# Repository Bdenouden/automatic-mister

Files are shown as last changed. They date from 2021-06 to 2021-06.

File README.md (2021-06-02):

# Mister automatic
An automated approach to misting my mushroom farm

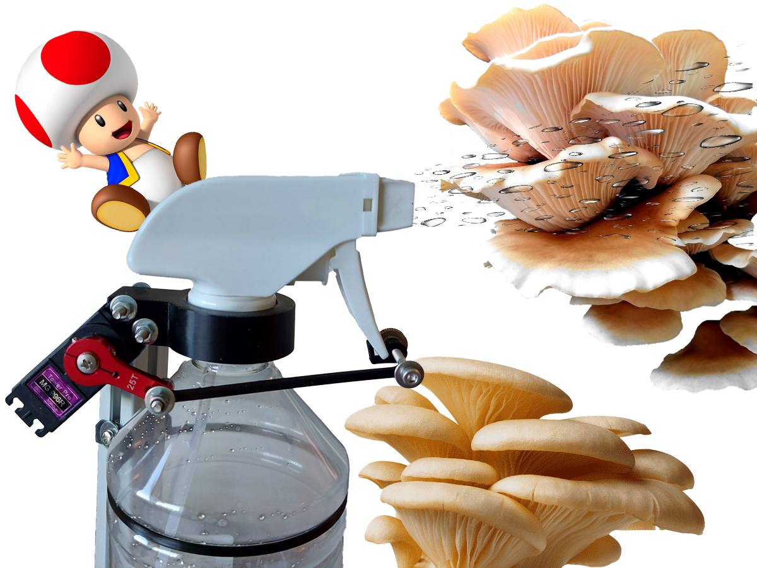
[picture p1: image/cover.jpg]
cover


## Introduction
For my birthday this year, I've received my own mushroom farm. 
This farm starts out as a block of mycelium but promises to turn into edible mushrooms in approximately 10 days. 
In order to do so, the mycelium should first be submersed in water for a couple of hours and misted twice a day until the mushrooms are ready. 
When starting this farm I completely forgot my upcoming 4 days away from home, which would most likely mean my mushroom farm would dry out.

Since it was too late to postpone the farm, a different solution had to be found to mist my mushrooms whilst I was away from home. 
Furthermore a solution had to be found and created within 4 days so there was no time to order new components.

## Design
The biggest problem was the amount of force required to activate the spray nozzle. The motor must obviously have enough torque but at the same time, the bottle should not move when the motor is activated.

Speaking of activation: this system should mist my mushrooms twice a day and each time it activates a couple of 'pumps' are required.
Preferably, there would also be a feedback to the user like emails or notifications to existing home automation sytems.
To obtain this behaviour, a wifi enabled microprocessor is required along with a small pcb to manage power distribution.

This problem is therefore divided into thre separate issues: 
- Selecting a sufficiently strong motor
- Designing a robust, preferably self-supporting system
- Controlling the system

At the end of this section, a proof of concept is evaluated. 

### Motor
To solve the first issue, the MG996R servo motor was used; a high torque metal gear servo. Although this motor has sufficient torque (11kg/cm @ 6V), it can draw up to 2.5A of current.

The servo horn I had available is a metal arm with a maximum arm of 2.5cm, reducing the max torque to 4.4kg.
A quick test using a portable luggage scale was performed to verify if this would be enough. 
Since approximately 2 kg is required to fully retract the spray nozzle arm, the combination of the MG996R servo motor and 2.5cm servo horn should be strong enough.

Besides the 6V stall torque, the 4.8V stall torque was also specified by the manufacturer: 9.4kg/cm.
Using a 5V source and the same 2.5cm servo horn should still result in a max torque of ~3.8kg. 

This is very usefull information since I don't have any 6V sources which can supply up to 2.5A laying around but I do have many 5V usb chargers which can easily handle up to 3A.

### CAD
The second problem had to be solved using CAD. To prevent the bottle moving when spraying, the force used to activate the spray had to come from a part which is attached to the spray head but does not move during spraying.
By manually spraying a bit, I figured the most sturdy part which satisfies above demands would be the screwcap of the bottle.

The body of the system was thus designed to mimic how a human holds the spray bottle but with some attachements added for the selected servo motor. 
The image below shows the assembly of the cad model and the servo motor.

In order to attach the servo horn to the spray lever, a small clip which just snaps onto said lever and an arm to couple the clip to the servo horn was designed as well. 
These models are not explicitly shown in this section but will be visible in later pictures.

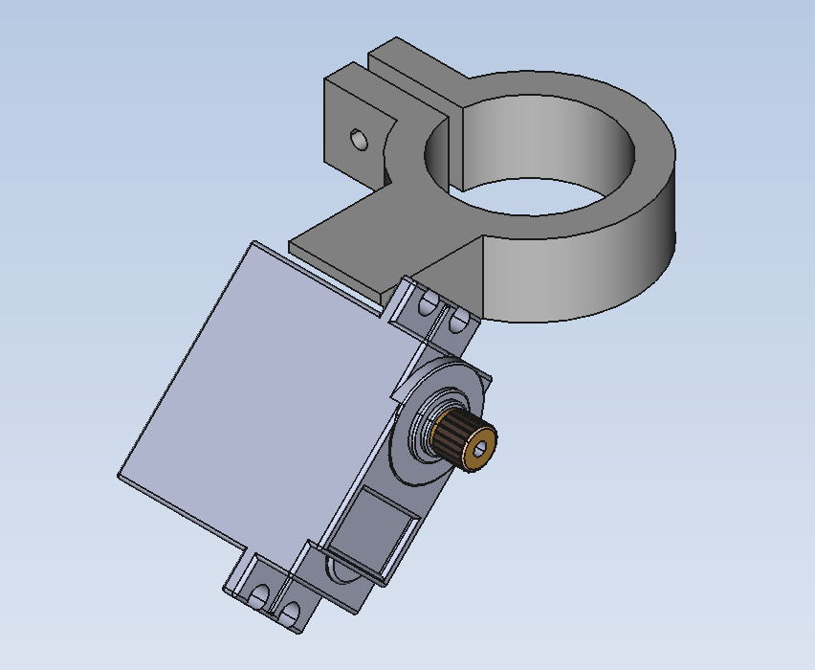
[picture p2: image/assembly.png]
Model of the CAD model and attached servo motor


### Controller
The controller consists of a ESP8266 based development board: the WEMOS D1 mini, a power distribution and a level shifter. 
The WEMOS D1 is a microctonroller with integrated wifi functionallity and functions as the brains of the system. 
It will send a signal to the servo when the motor must be activated. 
To ensure compatibillity, a level shifter has been put in between.
This shifts the 3.3V control signal to 5V, which is the supply voltage of the servo motor and also provides any drive current required. 

#### Power distribution
Although the WEMOS module has a 5V output, this pin can unfortunately not be used to power the servo motor. 
This is due to the schottky diode which is soldered in series with the usb input of the WEMOS: it can only handle up to 500mA continuously before releasing its magic smoke. 
Experiments using the servo motor have shown that it will easily exceed this maximum under load.
To prevent the schottky from burning through, a power distribution has been added:
- A micro USB connector is added for power input
- This power input is directly connected to the power supply pin of the servo motor and the '+' pins of the headers.
- The power input is connected to the 5V pin of the WEMOS module via a 'regular' 1N4001 diode.

Diode D1 is added to prevent the shottky diode on the WEMOS module from burning when the module is plugged into the computer. 
During programming the 5V pin of the module is attached to the usb power, without D1, the servo motor would become powered as well.
When power is supplied via J1 (the micro usb for power input) approximatley 4.3V is applied to the 5V pin.
This 5V pin is internally connected to a low dropout regulator with a maximum dropout voltage of 0.5V at full load
[[WEMOS D1 Mini schematic](https://www.wemos.cc/en/latest/_static/files/sch_d1_mini_v3.0.0.pdf), [LDO datasheet](https://datasheet.lcsc.com/szlcsc/Nanjing-Micro-One-Elec-ME6211C33M5G-N_C82942.pdf)].
Since the difference of input vs output voltage for this LDO is well above the dropout voltage, the 3.3V line of the WEMOS module will not be negatively affected by diode D1.

schematic design

<!-- TODO add firmware description -->

### Proof of concept
As a proof of concept, the designed models were printed and attached to the spray head of the bottle.
The controller was assembled on a breadboard, power was supplied by a controllable power supply.

The design functioned as intended and the maximum measured current draw was around 1.6A.

Issues requiring attention were:
1. Collision of the servo horn with the servo body
2. The nut attaching the 3d printed arm to the servo horn could undo itself over time
3. When the bolt attaching the spray lever to the 3d printed arm was tightened too much, the entire spray head would deform due to the angle at which the spray lever was pulled.

Issue 1 was solved by shortening the 3d printed arm by 5 mm. 
This placed the servo horn in a more horizontal position when the spray lever is uncompressed and vertically downwards when fully compressed, thus never hitting the servo body.

To fix issue 2 a self-locking nut was used on rotating parts and the third issue was fixed by simply not tightening said bolt. 
Although the spray head still deforms a bit, it's now comparable to when compressed by human hands. 

Something to watch out for is the deformation of the 3d printed arm.
A shown in the video, the rightmost hole is bent quite a bit which might cause it to break due to wear and tear over time.

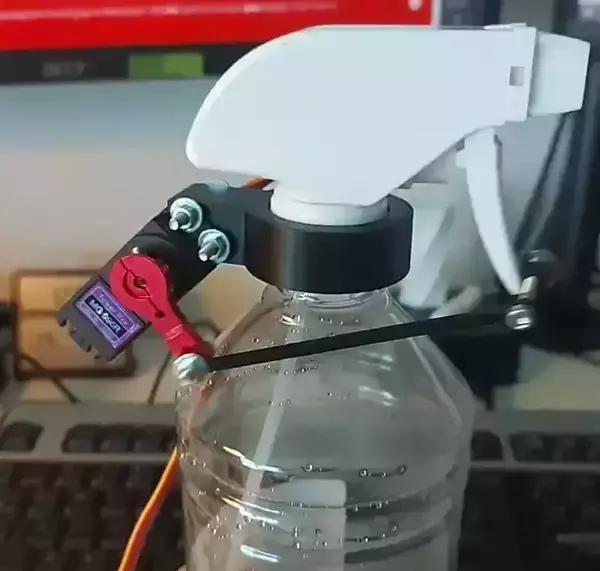
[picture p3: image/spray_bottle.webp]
proof of concept video


## Conclusion

The automatic mister was designed and assembled from stuff I had laying around within 2 days and is now completely assembled and functions as expected.
The remaining 2 days will be used to further test reliabillity of the system and spot possible weak points due to wear and tear.

Not only was the automatic mister constructed within time, it has been designed in a non-invasive way: No permanent modifications to the spray bottle or head are required to add the automation.

Although the system can operate without falling over (even without the bottle being full of water), I added a frame made out of aluminium extrusions for extra stabillity. 

Editable FreeCAD files, 3d printable AMF files and code are supplied via the github linked below.

### future work
Future work for this project is validation and refinement of the existing system:
- Tests over a longer period of time have to be performed to evaluate which parts will break first and what possible solutions might be.
- The spray head still slightly deforms due to the angle it is pulled at. This might be resolved by adding a secondary arm to the servo horn opposed to the current arm. A way to achieve this is to add a stable axis along which the servo horn(s) rotate when activated.
- The aluminum frame should be replaced by a smaller support to help stabilize it or the center of mass should be lowered.
- A PCB layout could be added to improve reliability of the controller.
- The ESP8266 is not a secure module. If this system is connected to a server which requires authentication, I highly recommend using devices like an esp32 which has flash encryption.
- A mosfet should be added to toggle the power supply of the servo motor. Not only will this save power, 99% of the time the servo motor is just waiting for instructions, it will also remove the need for finetuning the 'off' position of the servo. The spray lever is strong enough to retract to its prefered position when the servo motor has no power. As a result the servo motor wont have to use any force to combat the slight force which is applied by the lever when the position is slightly off.

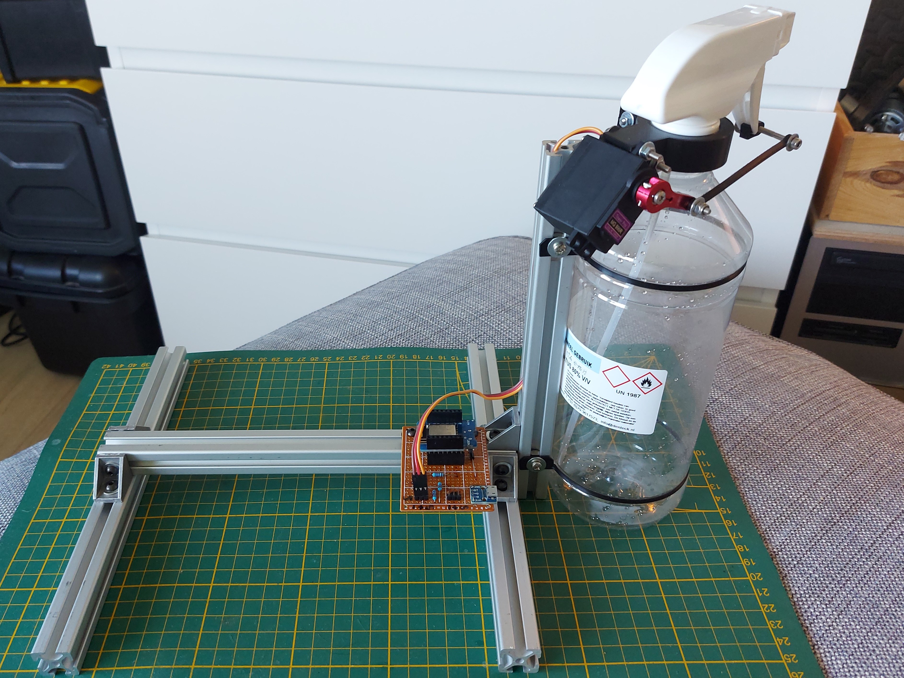
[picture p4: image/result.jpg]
Completed system


### Note
Please ignore the 'danger' and 'imflammable' labels on the spray bottle, this is what I had at hand and it has been cleaned thourouly, I promise!

### More info and code:



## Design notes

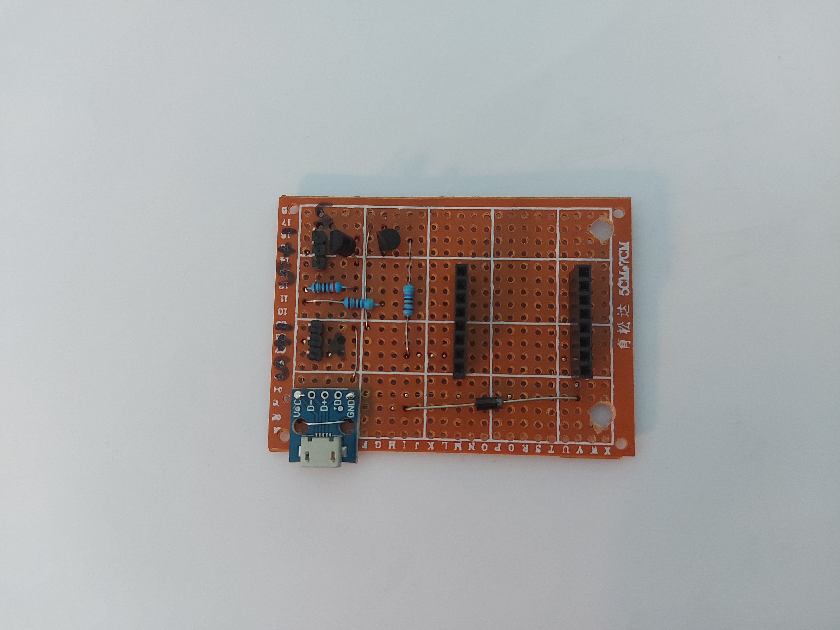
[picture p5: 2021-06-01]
image/pcb_no_esp.jpg

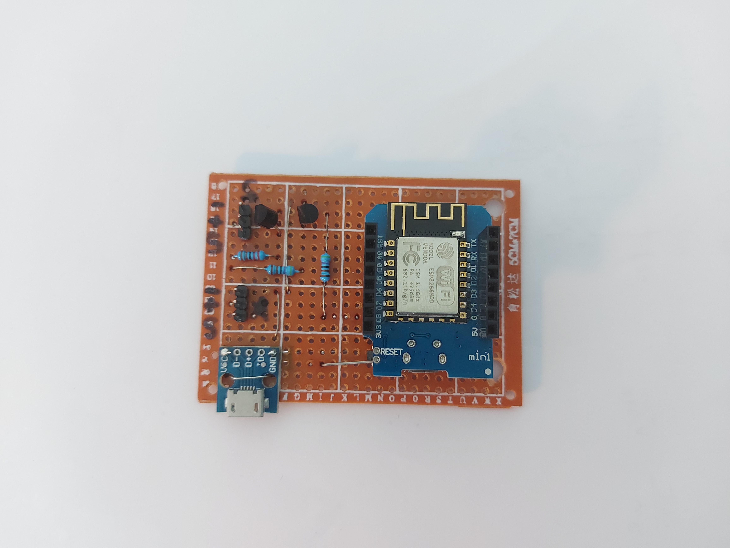
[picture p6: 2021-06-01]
image/pcb_esp.jpg

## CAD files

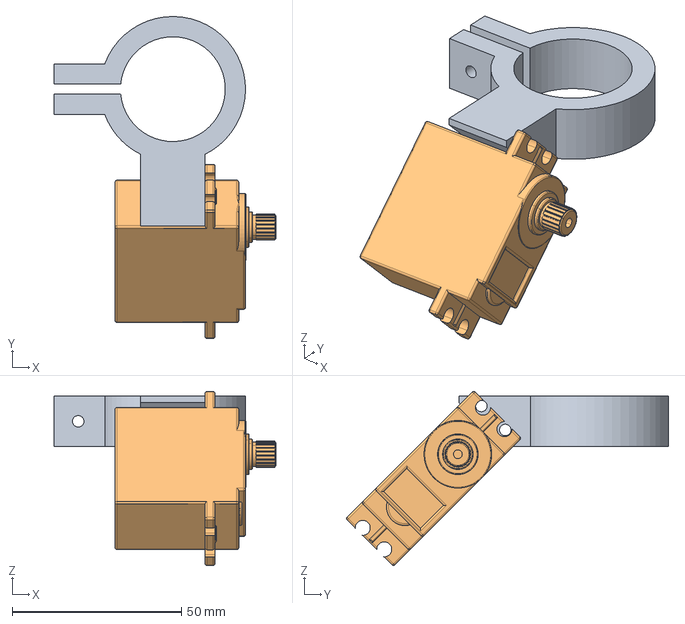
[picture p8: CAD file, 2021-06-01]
CAD/assembly.FCStd
65.6 x 95.3 x 51.5 mm
Servo MG996R1_001

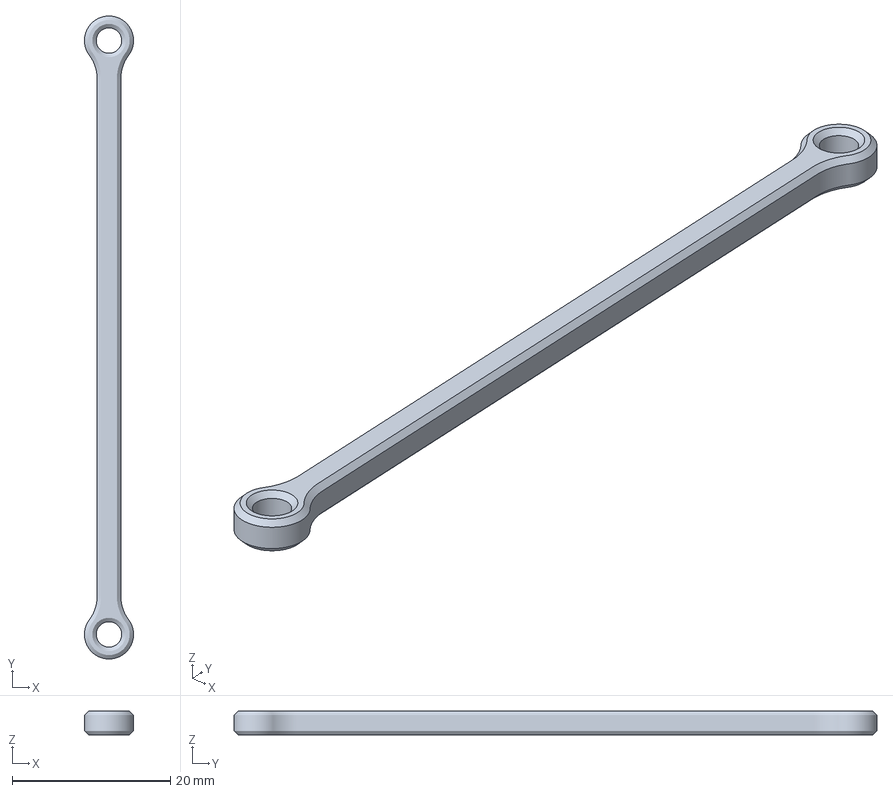
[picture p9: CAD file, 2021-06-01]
AMF/arm-75mm.amf
6.20 x 81.2 x 3.00 mm

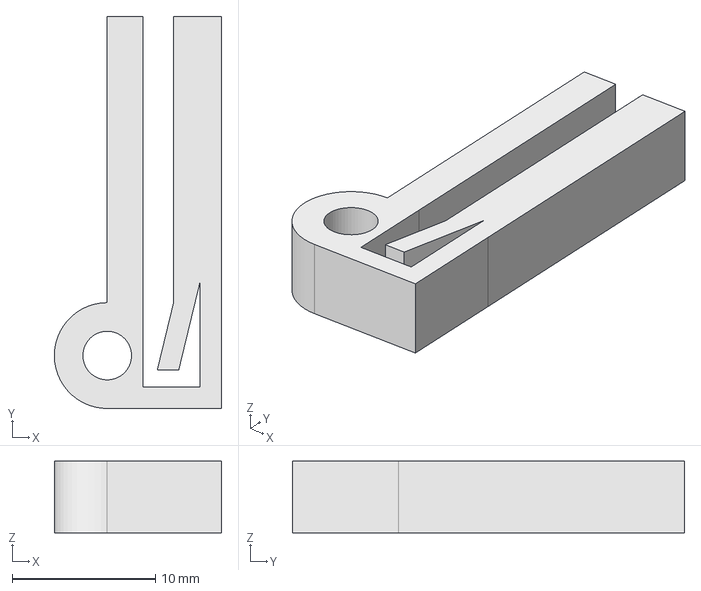
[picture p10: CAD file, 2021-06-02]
CAD/clip V2.FCStd
11.7 x 27.4 x 5.00 mm

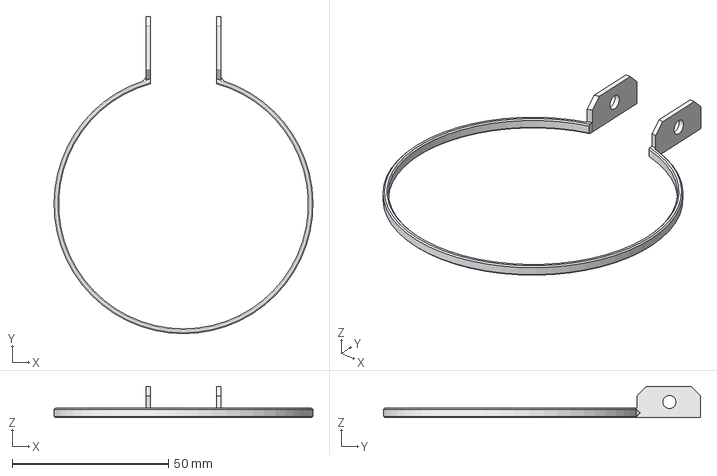
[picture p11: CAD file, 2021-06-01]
CAD/bottle_ring_2020.FCStd
83.0 x 101.6 x 10.0 mm

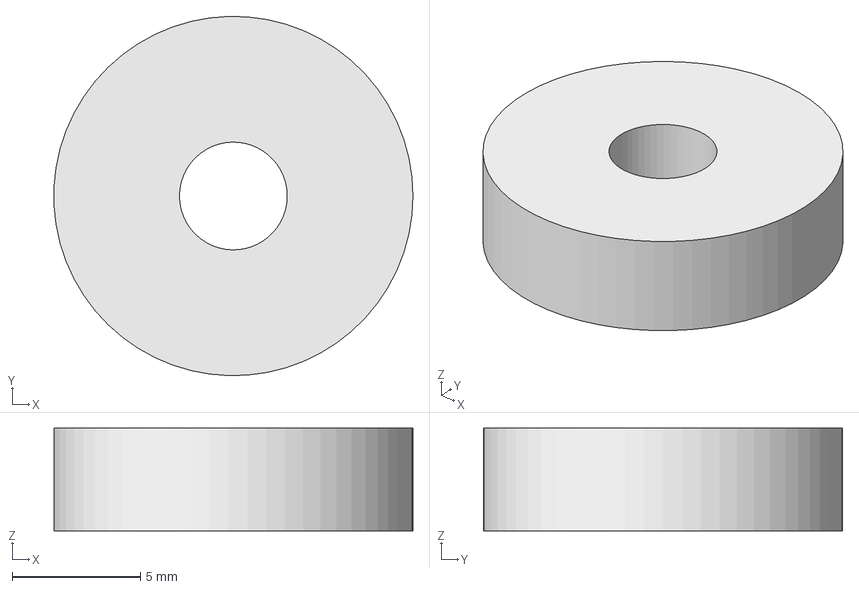
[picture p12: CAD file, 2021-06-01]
CAD/spacer.FCStd
14.0 x 14.0 x 4.00 mm

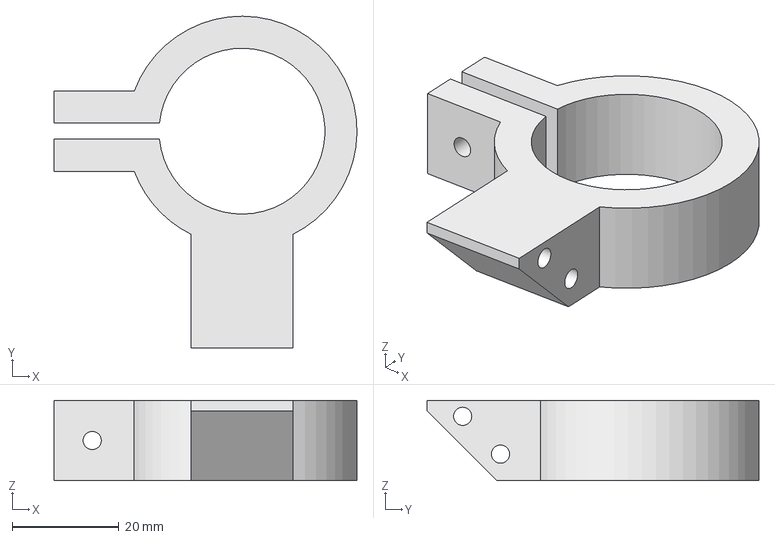
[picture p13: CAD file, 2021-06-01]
CAD/body.FCStd
56.6 x 62.0 x 15.0 mm

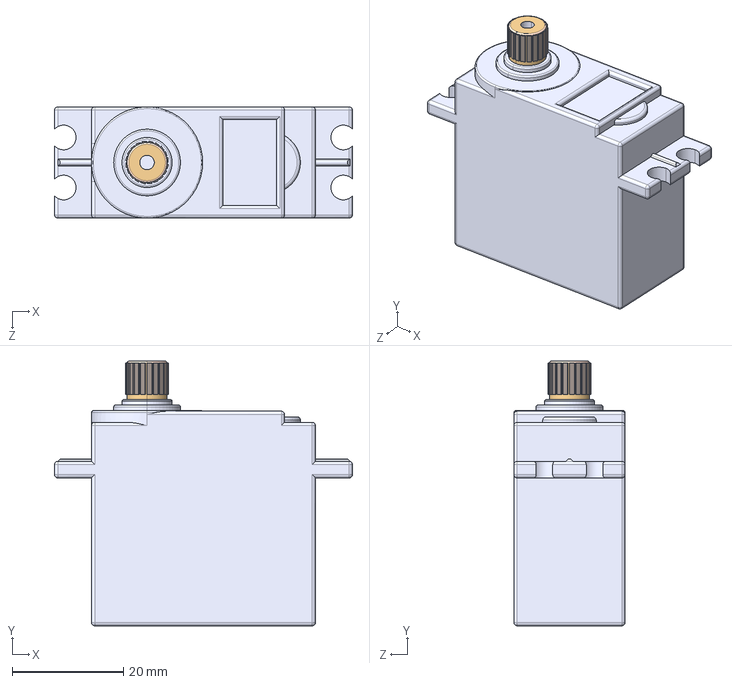
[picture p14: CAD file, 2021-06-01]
CAD/Servo MG996R.STEP
53.6 x 47.6 x 20.0 mm

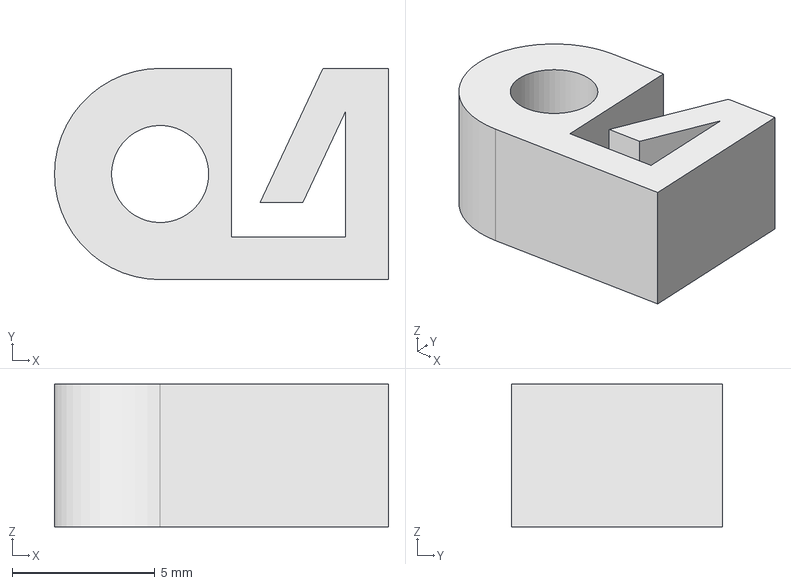
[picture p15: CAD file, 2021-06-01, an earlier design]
CAD/clip.FCStd
11.7 x 7.40 x 5.00 mm

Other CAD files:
CAD/arm.FCStd
AMF/body.amf
AMF/bottle_ring_2020.amf
AMF/clip V2.amf
AMF/clip.amf
AMF/spacer.amf

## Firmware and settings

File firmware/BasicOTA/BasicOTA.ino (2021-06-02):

/*
   OTA enabled firmware for the automatic mister https://github.com/Bdenouden/automatic-mister
   Based on the basicOTA example from the arduino ide

   Author: B. den Ouden
   02-06-2021
*/

#include <ESP8266WiFi.h>
#include <ESP8266mDNS.h>
#include <WiFiUdp.h>
#include <ArduinoOTA.h>
#include <NTPClient.h>
#include <Servo.h>
#include "configuration.h"  // user defined configuration

// 'credentials.h' stores your credentials based on the 'credentials.h.default' template
// The actual credentials.h should never be pushed to a version control system like git
#include "credentials.h"

// set wifi credentials to const char type
const char* ssid = STASSID;
const char* password = STAPSK;

// create and configure NTP object
WiFiUDP ntpUDP;
NTPClient timeClient(ntpUDP, NTP_SERVER, NTP_OFFSET, NTP_UPDATE);

// create servo object to control a serv
Servo servo;  


void setup() {
  Serial.begin(115200);
  Serial.println("Booting");
  WiFi.mode(WIFI_STA);
  WiFi.begin(ssid, password);
  while (WiFi.waitForConnectResult() != WL_CONNECTED) {
    Serial.println("Connection Failed! Rebooting...");
    delay(5000);
    ESP.restart();
  }

  // Port defaults to 8266
  // ArduinoOTA.setPort(8266);

  // Hostname defaults to esp8266-[ChipID]
  ArduinoOTA.setHostname("mister_automatic");

  // No authentication by default
  ArduinoOTA.setPassword(OTA_PASSWORD);

  // Password can be set with it's md5 value as well
  // MD5(admin) = 21232f297a57a5a743894a0e4a801fc3
  // ArduinoOTA.setPasswordHash("21232f297a57a5a743894a0e4a801fc3");

  ArduinoOTA.onStart([]() {
    String type;
    if (ArduinoOTA.getCommand() == U_FLASH) {
      type = "sketch";
    } else { // U_FS
      type = "filesystem";
    }

    // NOTE: if updating FS this would be the place to unmount FS using FS.end()
    Serial.println("Start updating " + type);
  });
  ArduinoOTA.onEnd([]() {
    Serial.println("\nEnd");
  });
  ArduinoOTA.onProgress([](unsigned int progress, unsigned int total) {
    Serial.printf("Progress: %u%%\r", (progress / (total / 100)));
  });
  ArduinoOTA.onError([](ota_error_t error) {
    Serial.printf("Error[%u]: ", error);
    if (error == OTA_AUTH_ERROR) {
      Serial.println("Auth Failed");
    } else if (error == OTA_BEGIN_ERROR) {
      Serial.println("Begin Failed");
    } else if (error == OTA_CONNECT_ERROR) {
      Serial.println("Connect Failed");
    } else if (error == OTA_RECEIVE_ERROR) {
      Serial.println("Receive Failed");
    } else if (error == OTA_END_ERROR) {
      Serial.println("End Failed");
    }
  });
  ArduinoOTA.begin();
  Serial.println("Ready");
  Serial.print("IP address: ");
  Serial.println(WiFi.localIP());


  pinMode(LED_BUILTIN, OUTPUT);

  // start NTP client
  timeClient.begin();
  
  // attaches the servo on the pin defined by SERVO_PIN to the servo object
  servo.attach(SERVO_PIN);  
}

// init both variables to invalid value
uint8_t hour = 99;
uint8_t prevHour = 99; // prevents multiple triggers within a single valid hour

void loop() {
  ArduinoOTA.handle();
  digitalWrite(LED_BUILTIN, !digitalRead(LED_BUILTIN));

  // get NTP time
  timeClient.update();
  Serial.println(timeClient.getFormattedTime());
  hour = timeClient.getHours(); // returns hours in 24h format

  if (hour != prevHour && hour == SPRAY_HOUR_1) {
    //    water round 1
    prevHour = hour;
    spray();
  }
  else if (hour != prevHour && hour == SPRAY_HOUR_2) {
    //    water round 2
    prevHour = hour;
    spray();
  }
  delay(5000);

}

// activate motor and spray plants
void spray()
{
  uint8_t pos;
  Serial.println("Now misting the farm");
  for (uint8_t pump = 0; pump < 5; pump++)
  {
      servo.write(0);
      delay(500);
      servo.write(110);
      delay(500);
      yield();
  }
}

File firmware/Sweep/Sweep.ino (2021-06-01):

/* Sweep
 by BARRAGAN <http://barraganstudio.com>
 This example code is in the public domain.

 modified 8 Nov 2013
 by Scott Fitzgerald
 http://www.arduino.cc/en/Tutorial/Sweep
*/

#include <Servo.h>

unsigned long time_old;

Servo myservo;  // create servo object to control a servo
// twelve servo objects can be created on most boards

int pos = 0;    // variable to store the servo position

void setup() {
  myservo.attach(D8);  // attaches the servo on pin 9 to the servo object
}

void loop() {
//  for (pos = 0; pos <= 120; pos += 1) { // goes from 0 degrees to 180 degrees
//    // in steps of 1 degree
//    myservo.write(pos);              // tell servo to go to position in variable 'pos'
////    delay(5);                       // waits 15ms for the servo to reach the position
//  }
myservo.write(0); // close
  delay(1000);

  //open
  for (pos = 0; pos <= 100; pos += 1) { // goes from 180 degrees to 0 degrees
    myservo.write(pos);              // tell servo to go to position in variable 'pos'
    delay(5);                       // waits 15ms for the servo to reach the position
  }

  time_old = millis();
  while(millis()-time_old <= 10000) yield();
  
}

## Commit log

2021-06-01 schematic design created
    [auto_mist.kicad_pcb, auto_mist.sch]
2021-06-02 opdateOTA basic firmware completed
    [configuration.h]
2021-06-02 clip V2 added
    [clip V2.FCStd, clip V2.amf]
2021-06-02 spray times moved to configuration
    [configuration.h]
